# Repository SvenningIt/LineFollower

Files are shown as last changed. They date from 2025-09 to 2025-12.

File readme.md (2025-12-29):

# LineFollower

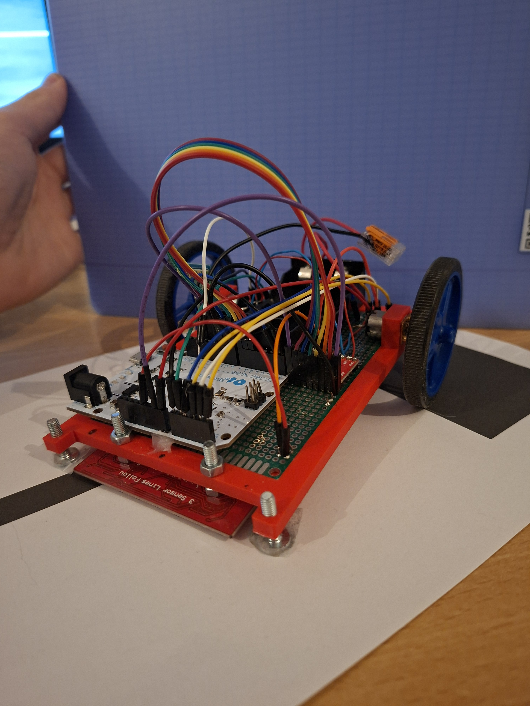
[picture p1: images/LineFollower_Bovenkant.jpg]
A description of my image


## specifications

microcontroller: Arduino Leonardo	atmega32u4

motors: Aslong DC-Transmissiemotor JGA12-N20-30 - 6V - 500RPM

h-bridge:	TB6612FNG

sensors: HY-S301

batteries: 	EVE ICR18650-26VA 2650mAh - 13A

wireless communication: HC-05 Wireless Module	RN-42

distance sensor - motors: 11cm

weight: 244g

speed: 0,74499 m/s

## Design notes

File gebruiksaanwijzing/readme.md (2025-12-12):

# Gebruiksaanwijzing

### opladen / vervangen batterijen
Vervang de batterijen indien ze leeg zijn van type 18650, de batterijhouder bevind zich op de achterkant van de linefollower.

### draadloze communicatie
#### verbinding maken
Download eerst de "Serial Bluetooth Terminal" app. Of een andere geschikte app, ik koos voor deze aangezien er macros ingesteld kunnen worden die het debuggen makkelijk maken. Steek de batterijen in de wagen en zet de bluetooth van je smartphone aan en maak verbinding met HC-05, de code is meestal 0000 of 1234 (In mijn geval 1234). Open de bluetooth serial terminal app en druk op het stekker icoontje rechtsboven.

#### commando's
debug [on/off]  
start  
stop  
set cycle [µs]  
set power [0..255]  
set diff [0..1]  
set kp [0..]  
set ki [0..]  
set kd [0..]  
set dAlpha [0..1]  
calibrate black  
calibrate white  

### kalibratie
Zet de wagen op een volledig zwart oppervlak en stuur het commando "calibrate black". Zet daarna de wagen op een compleet wit oppervlak en stuur het commando "calibrate white". 

### settings
De robot rijdt stabiel met volgende parameters:
Cycle time: 2500, Power: 190, diff: 0.45, kp: 14, ki: 0.03, kd: 0.3, dAlpha: 0.7

### start/stop button
De run on en off heb ik geimplementeerd in een macro op de bluetooth serial monitor app, heel simpel in te stellen door te houden op een vrije knop en het commando (run on/off) te schrijven. Ook heb ik dit gedaan voor het commando debug, heel handig voor rap de waardes te zien. De linefollower stopt vanzelf als die geen duidelijke zwarte lijn ziet.

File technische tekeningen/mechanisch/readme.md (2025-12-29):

Solidworks tekening voor het frame van de linefollower

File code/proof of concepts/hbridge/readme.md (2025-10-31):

# H-Bridge proof of concept

Meerdere grounds op de chip, maar 1 aangesloten.

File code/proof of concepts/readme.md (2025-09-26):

# Proof of Concepts

Een proof of concept is een combinatie van minimale hard- en software om eenvoudig aan te tonen dat iets werkt.  
Proof of concepts kunnen enerzijds als eerste poging dienen om een bepaald onderdeel van het project werkend te krijgen. Anderzijds kunnen ze tijdens het debuggen van het finale project dienen als test om eventuele hardware problemen te elimineren bij onduidelijke problemen.
<br />  
<br />
Een proof of concept bestaat uit
* een elektronisch schema (indien van toepassing)
* minimale code om de voorop gestelde zaken te demonstreren
* minimale uitleg / aandachtspunten
<br />
De elektronische schakelingen van de proof of concepts komen bij voorkeur overeen met deze van de uiteindelijke linefollower, zodat de code zonder aanpassingen op het finale project kan draaien.

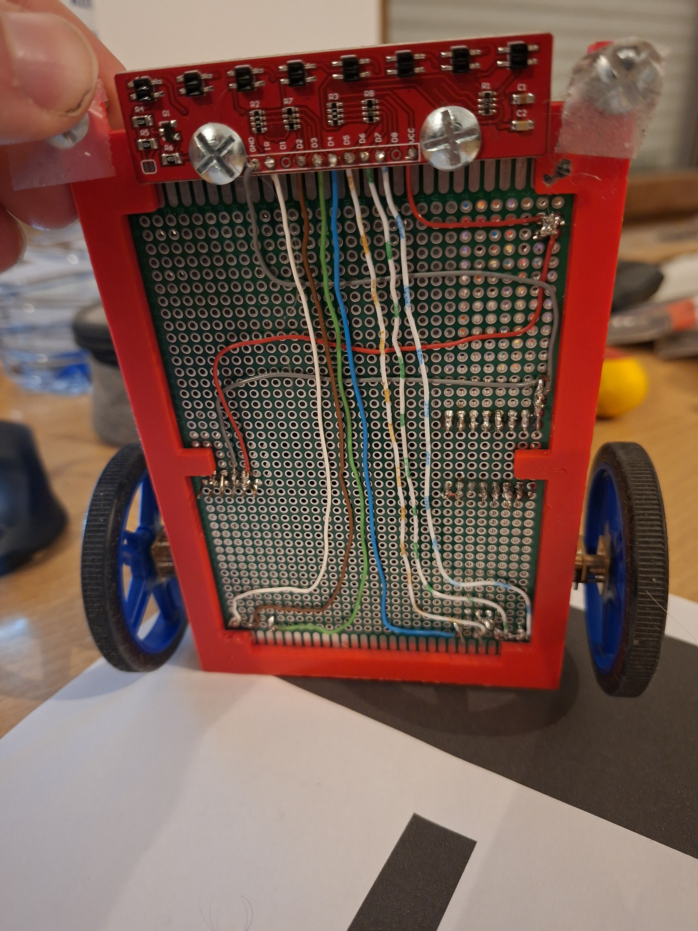
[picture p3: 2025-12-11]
images/LineFollower_Onderkant.jpg

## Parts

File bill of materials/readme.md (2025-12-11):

## bill of materials
<br />

|volgnummer|naam|omschrijving|nieuw/recup|kostprijs/stuk|aantal|subtotaal|
|---|----|---|---|---|---|---|
| 1 | Aslong DC-Transmissiemotor | JGA12-N20-30 - 6V - 500RPM | nieuw | €4,50 | 2 | €9,00 |
| 2 | 8x IR Lijn Tracking Module | HY-S301 | nieuw | €3,50 | 1 | €3,50 |
| 3 | Wielen | Pololu Wheel 60×8mm Pair - Blue | nieuw | €4,85 | 1 | €4,85|
| 4 | Dual Motor Driver | TB6612FNG | nieuw | €1,338  | 1 | €1,338  |
| 5 | HC-05 Wireless Module | RN-42 | nieuw | €3,80 | 1 | €3,80 |
| 6 | Arduino Leonardo | atmega32u4 | recup | €19,90  | 1 | €19,90  |
| 7 |Soldeerbord|PCB Board Prototype Board Green|nieuw|€1,63|1|€1,63|
|8|Batterijen|EVE ICR18650-26VA 2650mAh - 13A|nieuw|€1,45|2|€2,9|
|9|Batterij houder|18650 Batterijhouder met klemkontacten en losse draden|nieuw|€1,59|1|€1,59|
|10|Kabels|male to male en male to female|recup|€0,5|1|€0,5|
|Totaal||||||€49,008|

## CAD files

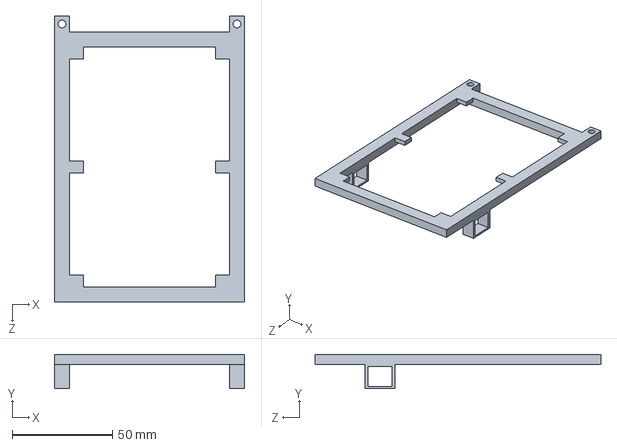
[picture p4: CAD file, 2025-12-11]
technische tekeningen/mechanisch/frame.SLDPRT
95.0 x 17.0 x 142.8 mm

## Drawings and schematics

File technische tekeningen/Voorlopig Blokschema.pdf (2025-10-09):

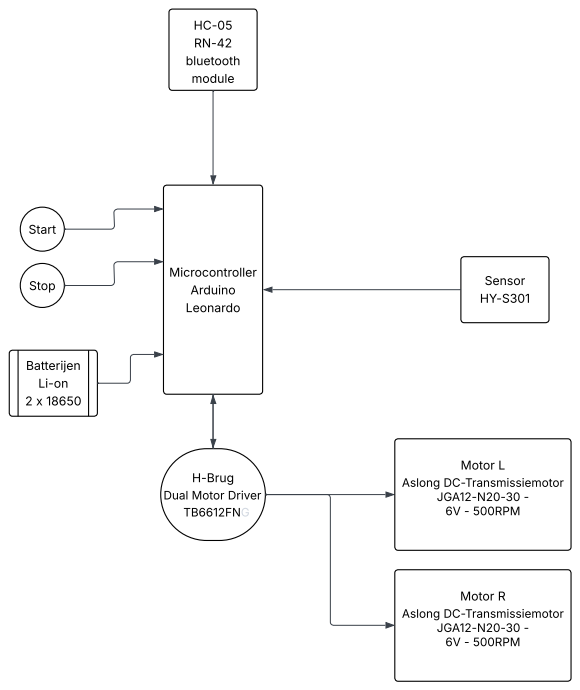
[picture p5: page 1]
Microcontroller Arduino Leonardo; H-Brug Dual Motor Driver TB6612FNG; Motor L Aslong DC-Transmissiemotor JGA12-N20-30 - 6V - 500RPM; Motor R Aslong DC-Transmissiemotor JGA12-N20-30 - 6V - 500RPM; Sensor HY-S301; HC-05 RN-42 bluetooth module; Batterijen Li-on 2 x 18650; Start; Stop

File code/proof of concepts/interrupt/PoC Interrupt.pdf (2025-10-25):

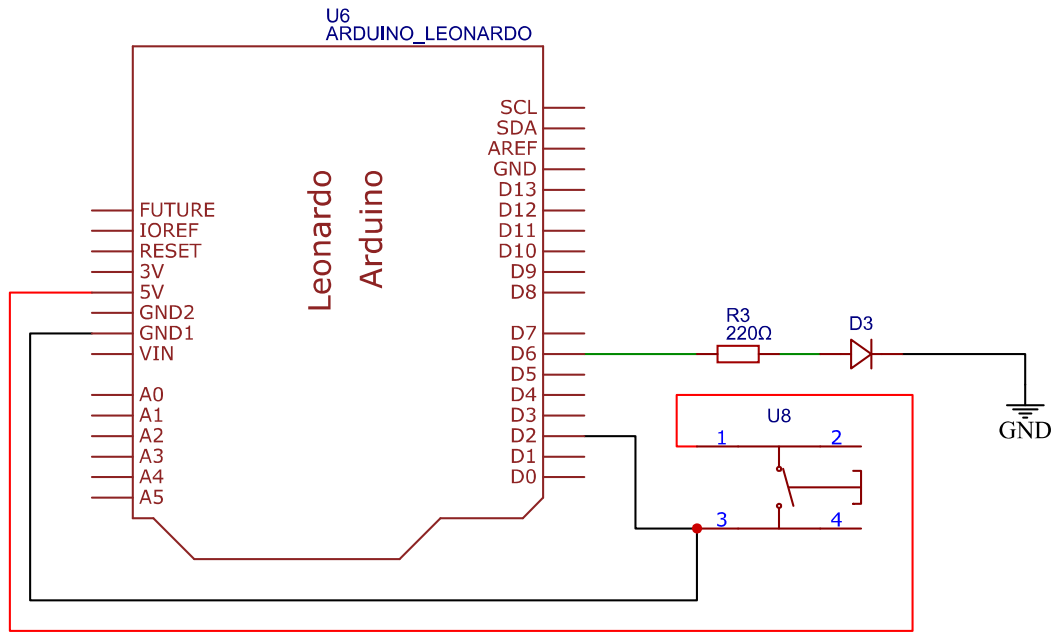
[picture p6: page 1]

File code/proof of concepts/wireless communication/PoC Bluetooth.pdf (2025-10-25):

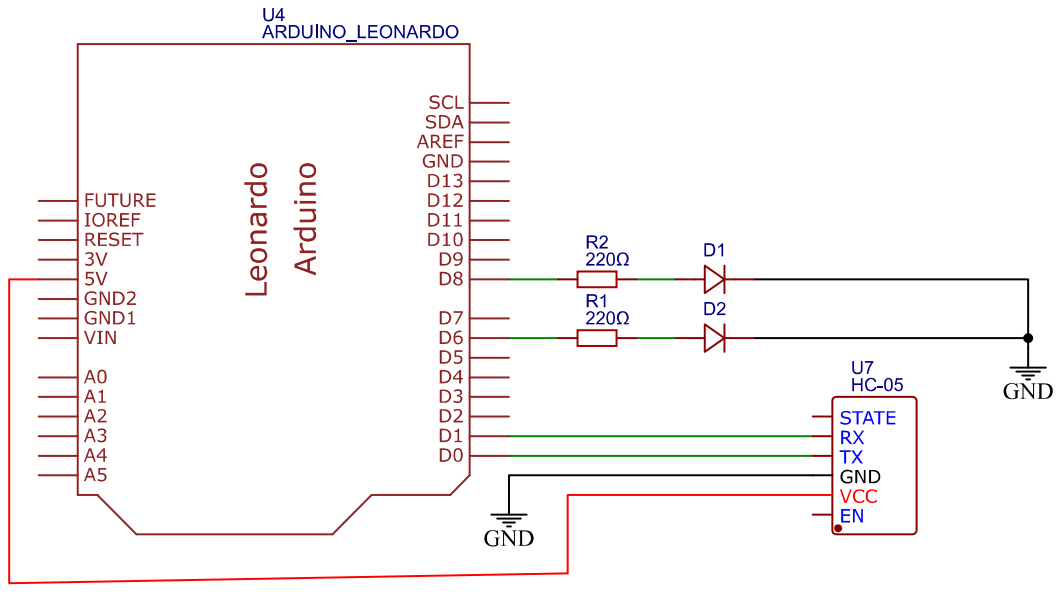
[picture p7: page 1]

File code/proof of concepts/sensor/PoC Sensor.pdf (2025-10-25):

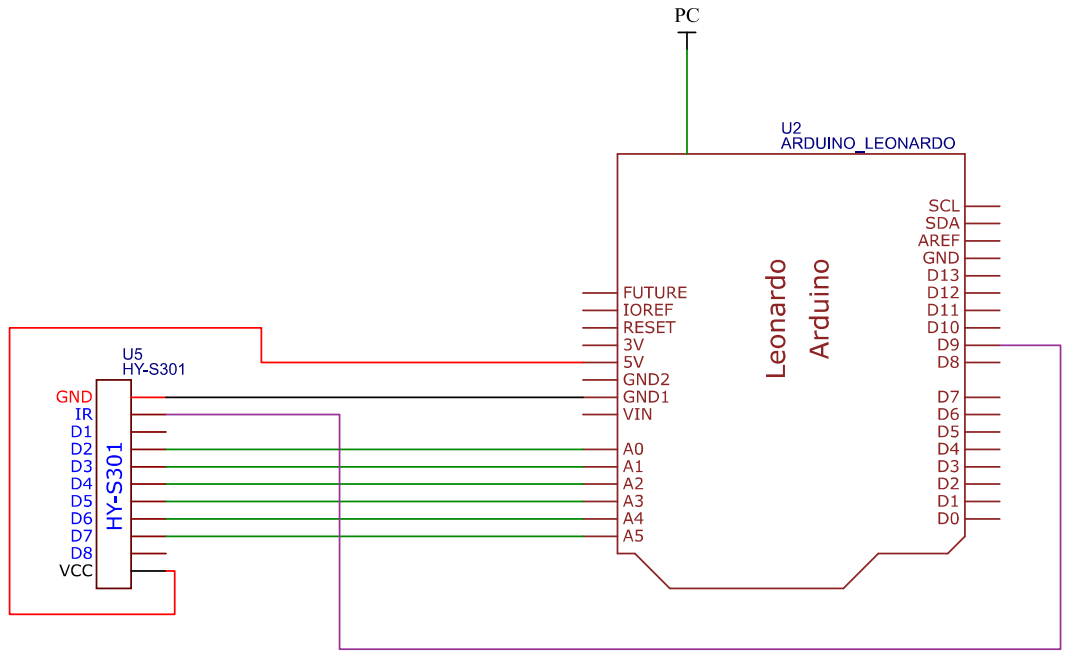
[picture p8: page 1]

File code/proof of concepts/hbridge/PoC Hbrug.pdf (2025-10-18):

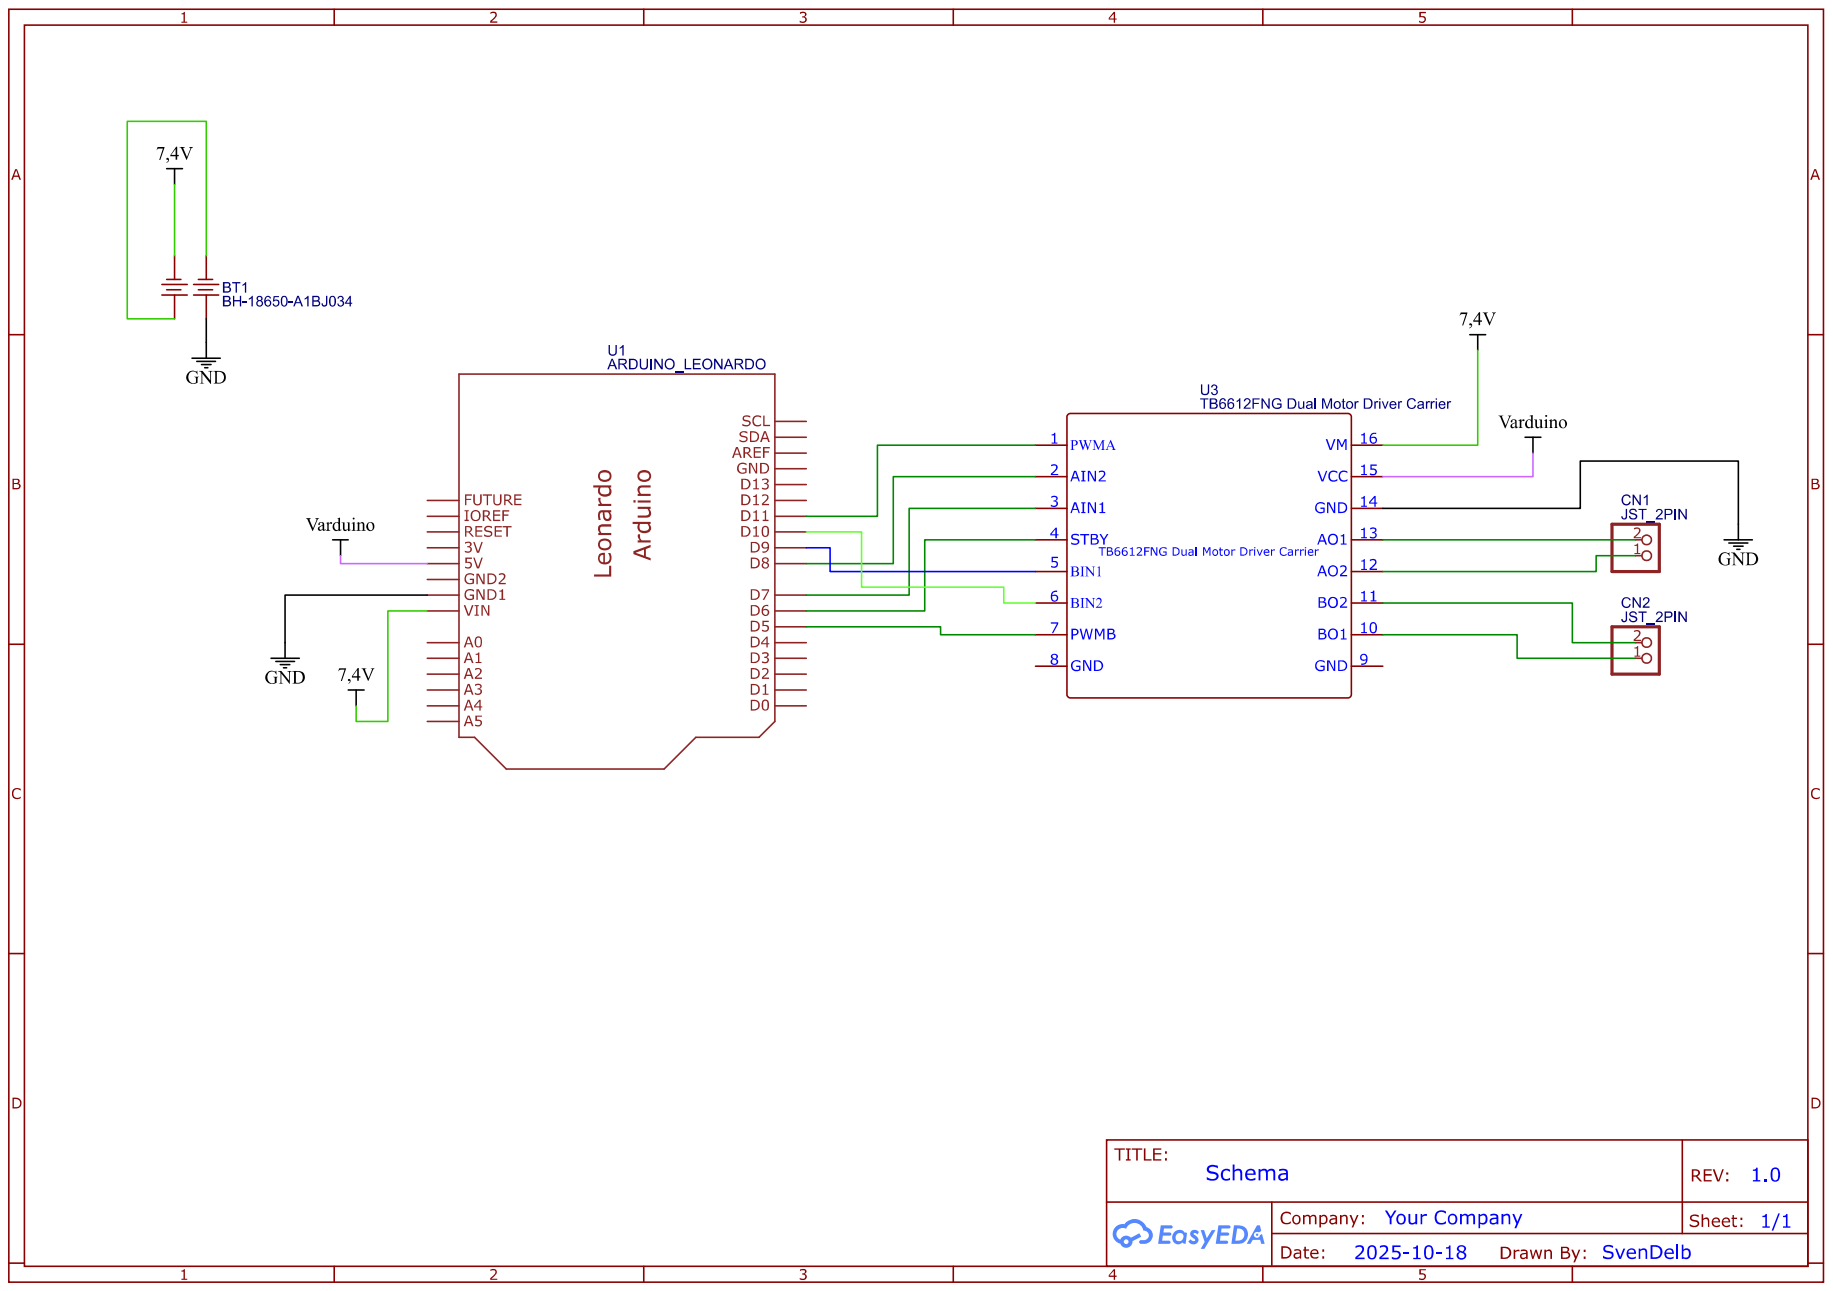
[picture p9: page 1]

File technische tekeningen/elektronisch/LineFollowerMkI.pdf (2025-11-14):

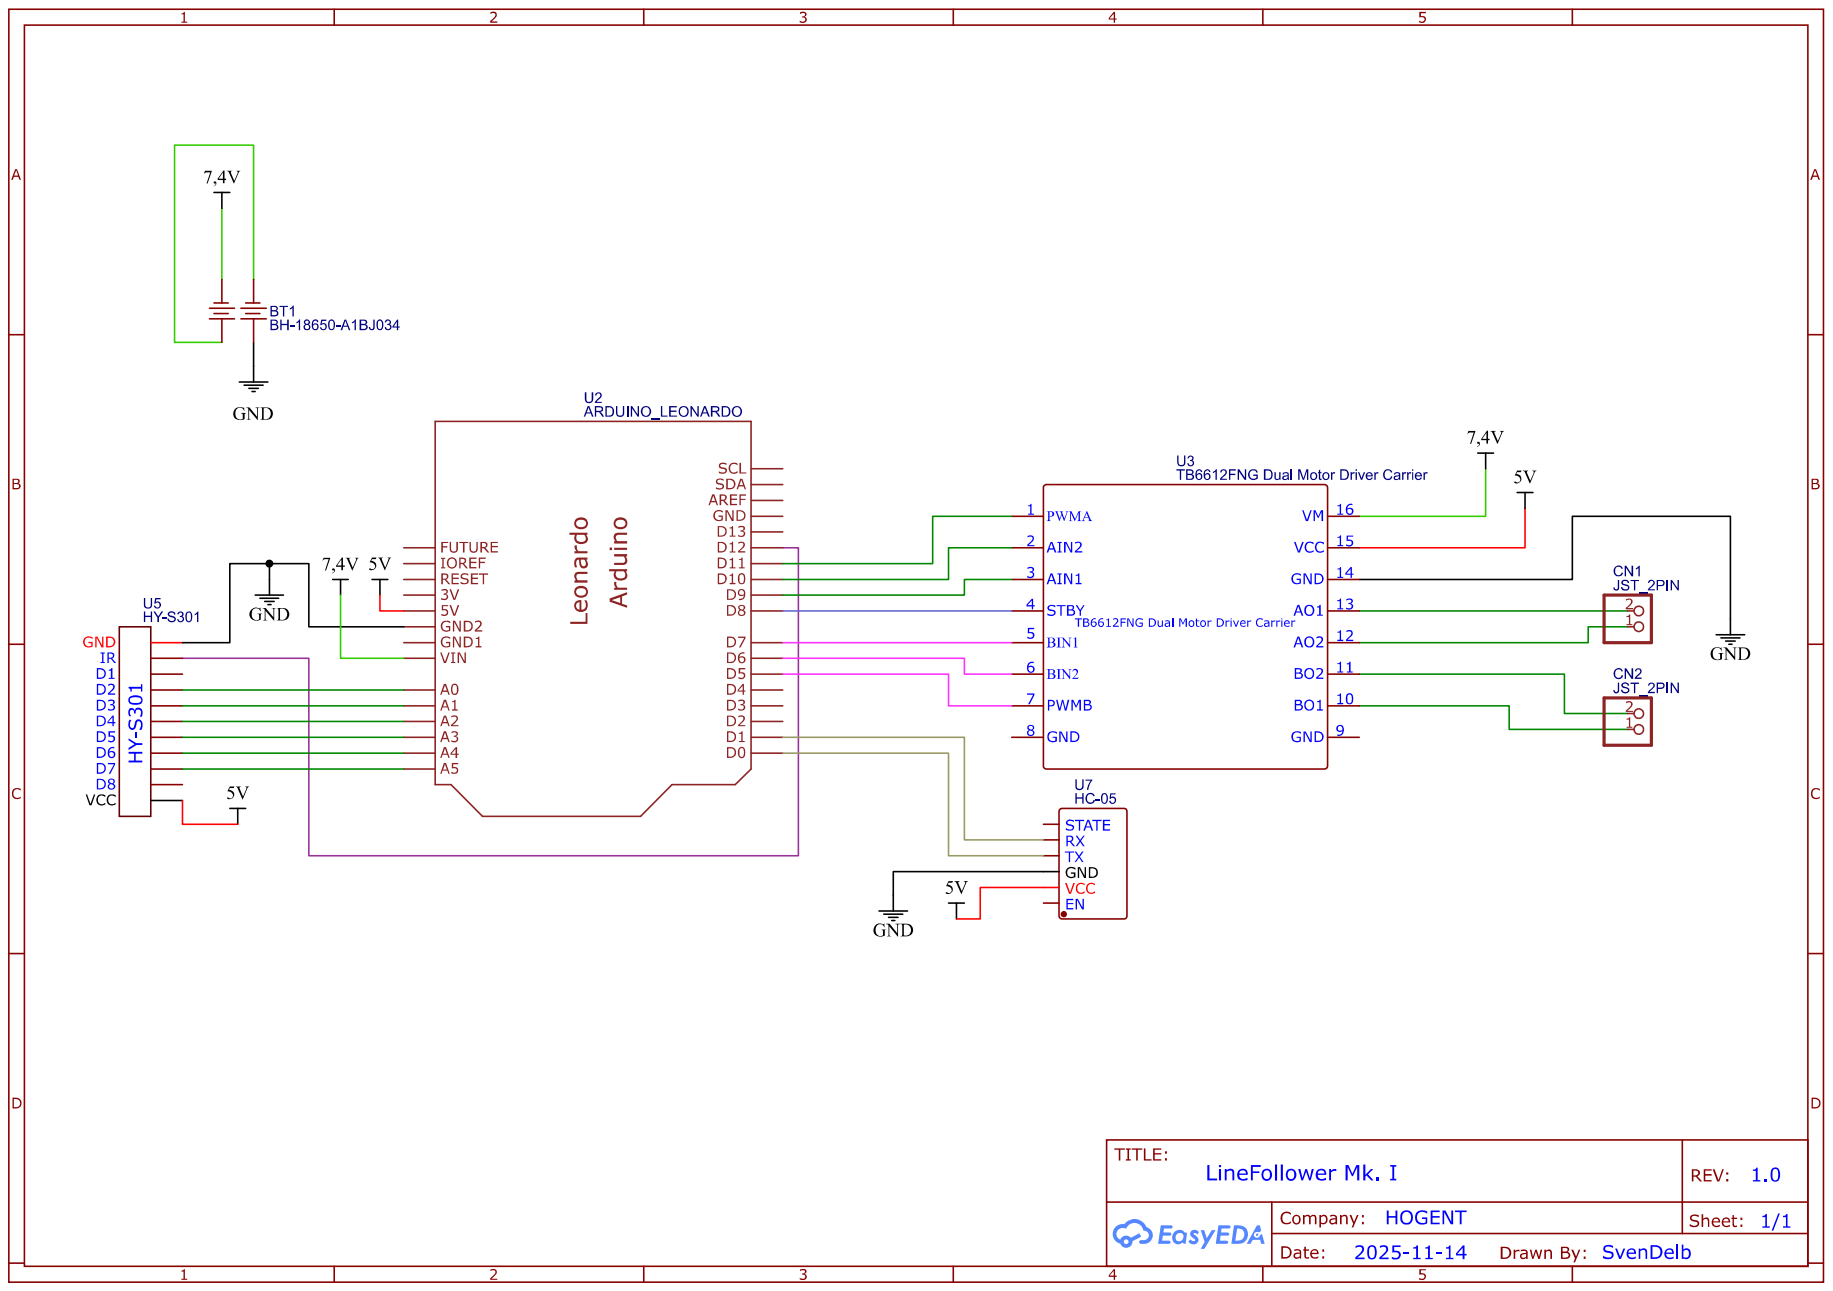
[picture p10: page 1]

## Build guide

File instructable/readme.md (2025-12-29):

# Instructable

### stap 1
Bestel alle benodigde componenten volgens de bill of materials.

### stap 2
3D-print het frame aan de hand van de mechanische tekeningen.

### stap 3
Boor twee gaten in de voorkant van het frame voor het indraaien van de bouten.

### stap 4
Plaats het soldeerbord in de daarvoor voorziene opening van het frame.

### stap 5
Soldeer de componenten en kabels op dezelfde posities als weergegeven op de foto.

### stap 6
Draai de bouten in de gaten die in stap 3 zijn geboord tot de opgegeven hoogte.

### stap 7
Plaats de batterijen in de houder, maar sluit de voeding van de batterijen naar de Arduino nog niet aan.

### stap 8
Laad het programma op de Arduino en verwijder daarna de USB-kabel van de pc.

### stap 9
Verbind de voedingskabel van de batterijen met de Arduino

### stap 10
Als beginwaarde voor de linefollower kun je de veilige waarden gebruiken die op de GitHub-pagina zijn vermeld. Van daaruit kun je verder experimenteren met nieuwe instellingen.

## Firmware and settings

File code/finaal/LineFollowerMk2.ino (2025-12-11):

#include "SerialCommand.h"
#include "EEPROMAnything.h"

#define SerialPort Serial1
#define Baudrate 9600

SerialCommand sCmd(SerialPort);
bool debug;
bool run;
unsigned long previous, calculationTime;
float iTerm;
float lastErr;
float filteredDeriv = 0; 


const int sensor[] = {A0, A1, A2, A3, A4, A5};

const int AIN1 = 9;
const int AIN2 = 10;
const int PWMA = 11;

const int BIN1 = 7;
const int BIN2 = 6;
const int PWMB = 5;

const int STBY = 8;

struct param_t
{
  unsigned long cycleTime;

  int black[6];
  int white[6];
  int power;
  float diff;
  float kp;
  float ki;
  float kd;
  float dAlpha;
  /* andere parameters die in het eeprom geheugen moeten opgeslagen worden voeg je hier toe ... */
} params;

int normalised[6];
float debugPosition;

void setup()
{
  SerialPort.begin(Baudrate);

  sCmd.addCommand("set", onSet);
  sCmd.addCommand("debug", onDebug);
  sCmd.addCommand("calibrate", onCalibrate);
  sCmd.addCommand("run", onRun);
  sCmd.setDefaultHandler(onUnknownCommand);

  EEPROM_readAnything(0, params);

  pinMode(13, OUTPUT);

  pinMode(AIN1, OUTPUT);
  pinMode(AIN2, OUTPUT);
  pinMode(PWMA, OUTPUT);

  pinMode(BIN1, OUTPUT);
  pinMode(BIN2, OUTPUT);
  pinMode(PWMB, OUTPUT);
  pinMode(STBY, OUTPUT);
  digitalWrite(STBY, HIGH);   // H-brug aan

  SerialPort.println("ready");
}

void loop()
{
  sCmd.readSerial();
 
  unsigned long current = micros();
  if (current - previous >= params.cycleTime)
  {
    previous = current;
    
    /* code die cyclisch moet uitgevoerd worden programmeer je hier ... */

    for (int i = 0; i < 6; i++)
    {
      normalised[i] = map(analogRead(sensor[i]), params.black[i], params.white[i], 0, 1000);
    }

    float position;
    int index = 0;
    for (int i = 1; i < 6; i++)if (normalised[i] < normalised[index]) index = i;

    if(normalised[index] > 800) run = false;
    
    if (index == 0) position = -30;
    else if (index == 5) position = 30;
    else
    { 
      int sNul = normalised[index];
      int sMinEen = normalised[index-1];
      int sPlusEen = normalised[index+1];

      float b = sPlusEen - sMinEen;
      b = b / 2;

      float a = sPlusEen - b - sNul;

      position = -b / (2 * a);
      position += index;
      position -= 2.5;

      position *= 15;
    }

    debugPosition = position;
    
    /*p regeling */
    float error = -position;
    float output = error * params.kp;

    /*i regeling */
    if (run) {
    iTerm += params.ki * error;
    iTerm = constrain(iTerm, -510, 510);
    output += iTerm;
    }   
    else {
    iTerm = 0;  // iterm resetten bij stoppen
    }

    /* d regeling*/

    float rawDeriv = error - lastErr;
    filteredDeriv = filteredDeriv * params.dAlpha + rawDeriv * (1.0 - params.dAlpha);
    output += params.kd * filteredDeriv;
    lastErr = error;

    output += iTerm;

  
    /* aansturen motoren */
    output = constrain(output, -510, 510);

    int powerLeft = 0;
    int powerRight = 0;

    if (run) if (output >= 0)
    {
      powerLeft = constrain(params.power + params.diff * output, -255, 255);
      powerRight = constrain(powerLeft - output, -255, 255);
      powerLeft = powerRight + output;
    }
    else //negatieve waardes van pos
    {
      powerRight = constrain(params.power - params.diff * output, -255, 255);
      powerLeft = constrain(powerRight + output, -255, 255);
      powerRight = powerLeft - output;
    }


    // Rechts
    digitalWrite(BIN1, powerRight > 0 ? HIGH : LOW);
    digitalWrite(BIN2, powerRight < 0 ? HIGH : LOW);
    analogWrite(PWMB, abs(powerRight));

    // Links
    digitalWrite(AIN2, powerLeft > 0 ? HIGH : LOW);
    digitalWrite(AIN1, powerLeft < 0 ? HIGH : LOW);
    analogWrite(PWMA, abs(powerLeft));

    

  }

  unsigned long difference = micros() - current;
  if (difference > calculationTime) calculationTime = difference;
}

void onUnknownCommand(char *command)
{
  SerialPort.print("unknown command: \"");
  SerialPort.print(command);
  SerialPort.println("\"");
}

void onSet()
{
  char* param = sCmd.next();
  char* value = sCmd.next();  
  
  if (strcmp(param, "cycle") == 0)
  {
    long newCycleTime = atol(value);
    float ratio = ((float) newCycleTime) / ((float) params.cycleTime);

    params.ki *= ratio;
    params.kd /= ratio;

    params.cycleTime = newCycleTime;
  }

  else if (strcmp(param, "ki") == 0)
  {
    float cycleTimeInSec = ((float) params.cycleTime) / 1000000;
    params.ki = atof(value) * cycleTimeInSec;
  }

  else if (strcmp(param, "kd") == 0)
  {
    float cycleTimeInSec = ((float) params.cycleTime) / 1000000;
    params.kd = atof(value) / cycleTimeInSec;
  }

  else if (strcmp(param, "dAlpha") == 0)
  {
    params.dAlpha = atof(value);
  }

  else if (strcmp(param, "power") == 0) params.power = atol(value);
  else if (strcmp(param, "diff") == 0) params.diff = atof(value);
  else if (strcmp(param, "kp") == 0) params.kp = atof(value);

  /* parameters een nieuwe waarde geven via het set commando doe je hier ... */
  
  EEPROM_writeAnything(0, params);
}

void onDebug()
{
  SerialPort.print("cycle time: ");
  SerialPort.println(params.cycleTime);
  
  /*parameters weergeven met behulp van het debug commando doe je hier ... */
  SerialPort.print("black: ");
  for (int i = 0; i < 6; i++)
  {
    SerialPort.print(params.black[i]);
    SerialPort.print(" ");
  }
  SerialPort.println(" ");

  SerialPort.print("white: ");
  for (int i = 0; i < 6; i++)
  {
    SerialPort.print(params.white[i]);
    SerialPort.print(" ");
  }
  SerialPort.println(" ");

  SerialPort.print("normalised values: ");
  for (int i = 0; i < 6; i++)
    {
      SerialPort.print(normalised[i]);
      SerialPort.print(" ");
    }
  SerialPort.println(" ");

  SerialPort.print("positie:");
  SerialPort.println(debugPosition);

  SerialPort.print("power: ");
  SerialPort.println(params.power);
  SerialPort.print("diff: ");
  SerialPort.println(params.diff);
  SerialPort.print("kp: ");
  SerialPort.println(params.kp);

  float cycleTimeInSec = ((float) params.cycleTime) / 1000000;

  float ki = params.ki / cycleTimeInSec;
  SerialPort.print("ki: ");
  SerialPort.println(ki);

  float kd = params.kd * cycleTimeInSec;
  SerialPort.print("kd: ");
  SerialPort.println(kd);

  SerialPort.print("dAlpha: ");
  SerialPort.println(params.dAlpha);

  SerialPort.print("calculation time: ");
  SerialPort.println(calculationTime);
  calculationTime = 0;
}

/*Sensor kalibreren op welke waarde wit/zwart zijn*/
void onCalibrate()
{
  char* param = sCmd.next();

  if (strcmp(param, "black") == 0)
  {
    SerialPort.print("start calibrating black... ");
    for (int i = 0; i < 6; i++) params.black[i]=analogRead(sensor[i]);
    SerialPort.println("done");
  }
  else if (strcmp(param, "white") == 0)
  {
    SerialPort.print("start calibrating white... ");    
    for (int i = 0; i < 6; i++) params.white[i]=analogRead(sensor[i]);  
    SerialPort.println("done");      
  }

  EEPROM_writeAnything(0, params);
}

void onRun() 
{
  char* parameter = sCmd.next();
  char* value = sCmd.next();
  if(strcmp(parameter, "on") == 0) 
  {
    run = true;
    iTerm = 0;
    lastErr = 0;
  }
  else run = false;
}

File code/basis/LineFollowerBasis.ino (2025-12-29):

#include "SerialCommand.h"
#include "EEPROMAnything.h"

#define SerialPort Serial
#define Baudrate 115200

SerialCommand sCmd(SerialPort);

unsigned long previous, calculationTime;
unsigned long blinkTimer = 0;
bool ledState = false;
bool run = true; // LED actief

// Magic number om EEPROM geldigheid te detecteren
#define EEPROM_SIGNATURE 0xBEEFCAFE

// Struct met parameters + handtekening
struct param_t
{
  unsigned long signature;       // herkenningswaarde
  unsigned long cycleTime;       // in microseconden
  unsigned long knipperPeriode;  // in milliseconden
} params;

// Functieprototypes
void onSet();
void onDebug();
void onUnknownCommand(char *command);
void start();
void stop();
void blinkSequenceSetup();

void setup()
{
  SerialPort.begin(Baudrate);

  // Commands
  sCmd.addCommand("set", onSet);
  sCmd.addCommand("debug", onDebug);
  sCmd.addCommand("start", start);
  sCmd.addCommand("stop", stop);
  sCmd.setDefaultHandler(onUnknownCommand);

  // Lees parameters uit EEPROM
  EEPROM_readAnything(0, params);

  // Controleer of EEPROM geldig is
  if (params.signature != EEPROM_SIGNATURE)
  {
    SerialPort.println("EEPROM leeg of ongeldig — initialiseer standaardwaarden");
    params.signature = EEPROM_SIGNATURE;
    params.cycleTime = 50000;       // 50 ms
    params.knipperPeriode = 1000;   // 1 s
    EEPROM_writeAnything(0, params);
  }

  pinMode(LED_BUILTIN, OUTPUT);
  blinkSequenceSetup();

  SerialPort.println("ready");
}

void loop()
{
  sCmd.readSerial();

  unsigned long current = micros();
  if (current - previous >= params.cycleTime)
  {
    previous = current;

    if (run)
    {
      blinkTimer += params.cycleTime / 1000; // µs → ms
      if (blinkTimer >= (params.knipperPeriode / 2))
      {
        ledState = !ledState;
        digitalWrite(LED_BUILTIN, ledState);
        blinkTimer = 0;
      }
    }
    else
    {
      digitalWrite(LED_BUILTIN, LOW);
    }
  }

  unsigned long difference = micros() - current;
  if (difference > calculationTime) calculationTime = difference;
}

// ===== Commando’s =====

void onSet()
{
  char* param = sCmd.next();
  char* value = sCmd.next();

  if (!param || !value) return;

  if (strcmp(param, "cycle") == 0)
  {
    params.cycleTime = atol(value);
  }
  else if (strcmp(param, "blink") == 0)
  {
    params.knipperPeriode = atol(value);
  }
  else
  {
    SerialPort.println("onbekende parameter");
    return;
  }

  // Bewaar in EEPROM
  EEPROM_writeAnything(0, params);
  SerialPort.println("parameter opgeslagen");
}

void onDebug()
{
  SerialPort.print("cycle time (us): ");
  SerialPort.println(params.cycleTime);
  SerialPort.print("blink periode (ms): ");
  SerialPort.println(params.knipperPeriode);
  SerialPort.print("run: ");
  SerialPort.println(run ? "true" : "false");
  SerialPort.print("calculation time (us): ");
  SerialPort.println(calculationTime);
  calculationTime = 0;
}

void onUnknownCommand(char *command)
{
  SerialPort.print("unknown command: \"");
  SerialPort.print(command);
  SerialPort.println("\"");
}

void start()
{
  run = true;
  SerialPort.println("knipperlicht gestart");
}

void stop()
{
  run = false;
  digitalWrite(LED_BUILTIN, LOW);
  SerialPort.println("knipperlicht gestopt");
}

// ===== Opstartsequentie =====
void blinkSequenceSetup()
{
  for (int i = 0; i < 3; i++) {
    digitalWrite(LED_BUILTIN, HIGH);
    delay(150);
    digitalWrite(LED_BUILTIN, LOW);
    delay(150);
  }
  delay(500);
}

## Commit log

2025-10-18 Add files via upload
    uitgemeten (alles zoals verwacht), in het echt werken de motoren niet via de h-brug, motoren draaien als ik ze aan de batterij zelf hang, elke ingangspin op de h-brug krijgt het juiste signaal, maar 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
2025-10-24 kleine pauze voor motor B
    onafhankelijkheid aantonen
2025-10-31 Update readme.md
    extra verklaring over de GND
2025-11-14 Elektronisch Schema voor de linefollower
2025-11-21 Change IR_LED pin from 8 to 9
2025-12-11 Foto's van de linefollower
2025-12-11 Finaal programma linefollower
    + de nodige bibliotheken
2025-12-11 Update bill of materials with new components and prices
2025-12-29 Interrupt Toegevoegd
2025-12-29 Add description for Solidworks frame drawing
